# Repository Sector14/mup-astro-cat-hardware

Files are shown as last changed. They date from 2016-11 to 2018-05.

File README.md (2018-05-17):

# MUP Astro CAT

The MUP Astro CAT is an auto GPIO configuring add-on board for the
Raspberry PI 3 which provides additional hardware interfaces to 
communicate and control a Meade Autostar, Moonlite focuser and
temperature sensors.

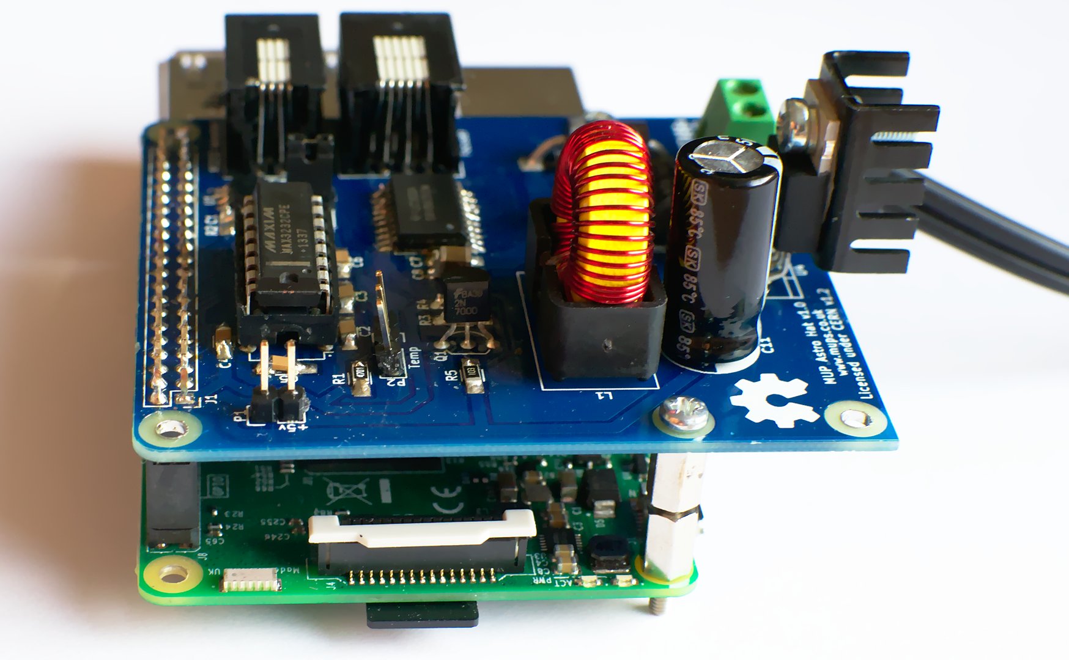
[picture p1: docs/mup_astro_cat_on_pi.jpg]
MUP Astro Hat


This repository contains the hardware project files needed to build 
the MUP Astro CAT. Firmware and the INDI driver is available in a separte
repo:

  https://github.com/Sector14/mup-astro-cat

Please refer to the additional documentation in the docs/ directory for
information on port pinouts for cables and hardware testing notes.

CAT refers to the Schmidt-Cassagrain telescope (CAT for short) this board will
be attached to. After naming it CAT I considered the recursive "CAP" which
would stand for "CAP Attached on Pi" since this project doesn't quite meet
the "Hat" spec, a cap is not a hat! but that means renaming things so CAT it is.

# Directories

  * control_cat - Kicad project incl schematic/pcb layout for the MUP Astro Cat. (CERN)
  * docs        - Documentation and 3rd party datasheets
  * gerber      - Exported gerber files for re-ordering PCBs

# Intended Purpose

Use a raspberry pi and additional interface board to control the 
following devices:

  * SXVR-H9
  * LodeStar
  * Filter Wheel
  * LX90 Handset
  * Moonlite Focuser
  * Illuminated Reticle (v2?)
  * Temp Sensor

The SXVR-H9, LodeStar (excl ST4 guide port) and Filter Wheel simply 
connect as USB devices to the Pi. 

The LX90 Handset uses a RS232 connection via RJ22 to the PI.

Moonlite focuser controlled via GPIO to a unipolar stepper
motor controller that will handle signal timing. Ensures any 
jitter/pauses from pi due to non realtime OS won't impact
motor control.

ST4 port from APM is not implemented, it might be added in a future
revision via i2c bus however as the LX90 supports pulse commands
over serial, it may not be needed.

# Library Setup

In addition to the libraries, modules and models that ship with Kicad,
this project also uses the MUP Kicad Library for additional parts and
an optional 3rd party 3D model library.

## Eeschema

If you receive a "The following libraries were not found:" message when
opening the schematic then you do not have the MUPS Kicad library available.
Kicad will use a cached copy of the library so this step is optional, but 
if you wish to make changes you should clone the repo:

  https://github.com/Sector14/mup-kicad-library

and add its location "Preferences/Component Libraries" as a user defined 
search path in the "parts library editor".  Then close and re-open Eeschema
and all the schematic symbols should now be found.

## Footprints

The above repo also contains footprint files for PCBNew in the modules/
directory and 3d models (where applicable). PCBNew will need each modules/\*.pretty
directory adding to the global library, or if you prefer, the project specific 
libraries.

To do so, open PCBNew, "Preferences/Footprints Libraries Manager", then 
"Append with Wizard" and select each ".pretty" directory and click Next, then
select whether to add the footprint to the global or project library.

Note: Some footprints are unchanged Kicad footprints that have only been
saved to the MUPS library in order to associate a 3d model with the footprint.
If the official Kicad library ever adds the missing models, the parts will
likely be removed from this repo.

## 3d Models

Some parts include a reference to models from the GPL'd 3d library by "kcswalter".
These are optional models and not included in the MUPS Kicad library.

If you checkout the walter repo from

  git://smisioto.eu/kicad_libs.git 

You can have Kicad use these models during 3d preview mode
by adding a new env variable in PCBNew "Preferences/Configure Paths" 
called WALTER_KI3DMOD and with the path set to the 
<walter repo checkout path>/modules/packages3d/ directory. 

Any footprints in the MUPS library that has the 3d model path prefixed 
with {WALTER_KI3DMOD}/walter/ will then use the appropriate 3D model.
The same will apply to {MUPS_KI3DMOD}/mups/ although at this time I've
yet to create any custom 3D models and find it unlikely I will

# Gerber Export

For Ordering PCBs from dirtypcbs.com

For "plotting":-

  * "Gerber" format is selected.
  * Select Layers F.Cu, B.Cu, F.SilkS, B.Mask, F.Mask, Edge.Cuts
  * Select Options:
   * Plot footprint values
   * Plot footprint references
   * Exclude PCB edge layer from other layers
  * Select Gerber Options:
   * User Protel filename extensions

For Drill file:

  * Units Inches
  * Zeros Format, Suppress leading zeros
  * Drill Map File Format (not used)
  * Drill File Options:
   * Minimal header
   * Merge PTH and NPTH holes into one file
  * Drill origin, Absolute

After export, rename the edge cuts "gm1" extension to "gml" prior
to uploading zip to dirtypcbs.com.

# Future Revision

Selecting surface 1206 style footprint for C8, the 100uF bypass capacitor 
for the DRV8805 was a little costly due to needing higher than 12V. An 
SMD electrolytic would prove significantly cheaper £0.27 vs £2.46
and with a greater voltage margin and not require that much additional 
space for a radial footprint. Lapse in judgement to be corrected on a 
future revision.

The power supply could be reduced in size with a more carefully
selected inductor. Having never laid out a SMPS however, I decided
to stick to the recommended layout and inductors based on the
TI regulator used. Further experimentation will be done prior to
revision 2 along with a change to SMD electrolytics and diodes.

A surface mounting socket to mate the CAT to the pi would be a better
choice as it allows an extended pin leg header to be mounted to the
pi and then the CAT mounted on top. This works out cheaper than the
elevated sockets.

Signal lines all need test point locations making available.

Switch 4p4c and 6p6c connector layout to socket mounting 
to allow panel mount option or in the case of a direct wiring, a
smaller connector area.

USB ideally should also be panel mount but desoldering the PI's
dual sockets is something I'd prefer to avoid.

ST3232 switch to soic version.

Add pin labels to silkscreen for temp port etc current broken square for
ground is too hard to see once a pin header is soldered in place.

Add a via behind the regulator to connect ground planes for better
thermal relief.

HAT specs for back-powering via 5V GPIO header pin requires addition
of an ideal 'safety' diode see [design guide](https://github.com/raspberrypi/hats/blob/master/designguide.md)

# Reference

  * https://github.com/raspberrypi/hats
  * https://github.com/raspberrypi/hats/blob/master/designguide.md
  * https://github.com/xesscorp/RPi_Hat_Template
  * http://www.briandorey.com/post/Raspberry-Pi-3-UART-Boot-Overlay-Part-Two

# Copyright

Copyright Gary Preston 2016.

This documentation describes Open Hardware and is licensed under the
CERN OHL v. 1.2.

You may redistribute and modify this documentation under the terms of the
CERN OHL v.1.2. (http://ohwr.org/cernohl). This documentation is distributed
WITHOUT ANY EXPRESS OR IMPLIED WARRANTY, INCLUDING OF
MERCHANTABILITY, SATISFACTORY QUALITY AND FITNESS FOR A
PARTICULAR PURPOSE. Please see the CERN OHL v.1.2 for applicable
conditions

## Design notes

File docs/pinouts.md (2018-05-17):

# Pinouts

## Pi Hat RS232

Looking into port, locking tab on bottom, left to right:-

  1. GND
  2. NC
  3. Tx
  4. Rx

## Autostar RS232 Port

Looking into port with locking tab on bottom, left to right:- 

  * GND
  * NC
  * Tx
  * Rx

Note: Tx and Rx should cross over in cable so Tx on PC is Rx on Autostar.

## Moonlite Focuser

    Model: LSG35012F76P
    Voltage: 12v
    Resistance/Phase: 65.0 Ohm
    Inductance H/Phase: 27.0
    Hold Current: 0.369A
    Total Input Watt: 4.5
    Min Holding Torque: 420 gf-cm (6.3 oz/in)
    Pull out Torque @ 175p/s: 151 gf-cm (2.1 oz-in)
    Detent Torque: 130 gf-cm (1.8 oz-in)
    Rotor inertia: 6.8 gf-cm^2 (0.372 oz-in^2)
    Weight: 82g (2.9oz)
    Length: 22mm (0.866in)

|Part No.     | Similar | Step Angle Degrees | Steps Per Revolution | Reduction | Nominal Voltage VDC | Min Holding Torque (oz-in)| Pull-out Torque @175p/s (oz-in) | Detent Torque (oz-in) | Rotor Inertia (oz-in) | Weight (oz) | Length (in) |
|LSG35012F76P |3004-003 |0.100 |3600 |75 |12 |150 |101 |150.0 |0.0372 |8.6 |1.55

Looking into 6p6c port on Pi Hat, locking tab on bottom, left to right:-

  1. 12v
  2. Out1
  3. Out2
  4. Out3
  5. Out4
  6. No connect

The moonlite focuser uses a DB9 connector with the following pin mapping:-

  1. O1 (coil 1+)
  2. O2 (coil 1-)
  3. O3 (coil 2+)
  4. O4 (coil 2-)
  5. 12v
  6-9 NC

The cable itself however cannot be a straight out1 -> O1, out2 -> O2 connection
as the stepping sequence the motor expects uses a different coil connection to the
out1..4 sequence. The cable needs to be:-

  Board Side -> DB9 Side
  1. 12v  -> 12v
  2. Out4 -> O3
  3. Out3 -> O2
  4. Out2 -> O4
  5. Out1 -> O1

           > DB9 Side
  1. 12v  -> 12v
  2. Out1 -> O1
  3. Out2 -> O4
  4. Out3 -> O2
  5. Out4 -> O3

# Reference

  * http://www.beckwithelectronics.com/HURST/LSG35012F76P.htm
  * http://www.weasner.com/etx/techtips/2007/aux-port.html
  * http://www.weasner.com/etx/archive/mar12/autostar.html

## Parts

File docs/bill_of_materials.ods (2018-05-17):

MUP Astro Hat V1.0 – Bill of Materials
Reference | Value | Qty | Footprint | Datasheet | Cost/item | Mouser | Farnell | Toby | Sparkfun
C1-C7,C10 | 0.1uF | 8 | Capacitors_SMD:C_1206_HandSoldering |  | £0.07 | 581-12065C104K |  |  |  |  | £0.56
C8 | 100uF | 1 | Capacitors_SMD:C_1206_HandSoldering |  | £2.95 |  | 2309033 |  |  |  | £2.95
C9 | 100uF | 1 | Capacitors_ThroughHole:C_Radial_D6.3_L11.2_P2.5 |  |  |  |  |  |  |  | £0.00 | already in stock
C11 | 1000uF | 1 | Capacitors_ThroughHole:C_Radial_D10_L16_P5 |  |  |  |  |  |  |  | £0.00 | already in stock
D2,D3 | 1N5822 | 2 | Diodes_ThroughHole:Diode_DO-201AD_Horizontal_RM15 |  | £0.14 |  | 9801243 |  |  |  | £0.28
J1 | RPi_GPIO | 1 | mups_connect:PI_Pin_Header_Straight_2x20 |  |  |  |  |  |  |  | £0.00
JP1 | Jumper_NO_Small | 1 | Connect:PINHEAD1-2 |  |  |  |  |  |  |  | £0.00 | already in stock
L1 | 100uH | 1 | mups_assorted:Choke_Toroid_8x16mm_Vertical |  | £4.32 |  | 2215967 |  |  |  | £4.32
P1 | 5V Reticle | 1 | Pin_Headers:Pin_Header_Straight_1x02 |  |  |  |  |  |  |  | £0.00 | already in stock
P2 | DS18B20 | 1 | Pin_Headers:Pin_Header_Straight_1x03 |  |  |  |  |  |  |  | £0.00 | already in stock
P3 | LX90 HBX | 1 | mups_connect:4P4C |  | £0.55 | 571-1-1705949-1 |  |  |  |  | £0.55
P4 | Focuser Motor | 1 | mups_connect:6P6C |  | £0.14 | 806-MP66X-1000 |  |  |  |  | £0.14
P5 | 12V In | 1 | mups_connect:Terminal_Block_5mm_2 |  | £0.26 | 571-282836-1 |  |  |  |  | £0.26
Q1 | 2N7000 | 1 | TO_SOT_Packages_THT:TO-92_Inline_Wide |  |  |  |  |  |  |  | £0.00 | already in stock
R1 | 4k7 | 1 | Resistors_SMD:R_1206_HandSoldering |  | £0.02 | 667-ERJ-8ENF4701V |  |  |  |  | £0.02
R2-R5 | 10k | 4 | Resistors_SMD:R_1206_HandSoldering |  | £0.05 | 588-AS12J1002ET |  |  |  |  | £0.20
R6 | 3k1 | 1 | Resistors_SMD:R_1206_HandSoldering |  | £0.01 |  | 2138387 |  |  |  | £0.01
R7 | 1k | 1 | Resistors_SMD:R_1206_HandSoldering |  | £0.05 | 588-AS12J1001ET |  |  |  |  | £0.05
U1 | 24C32 | 1 | Housings_SOIC:SOIC-8_3.9x4.9mm_Pitch1.27mm |  | £0.35 | 698-CAT24C32WI-GT3 |  |  |  |  | £0.35
U2 | ST3232 | 1 | Housings_DIP:DIP-16_W7.62mm |  | £6.07 |  | 2511858 |  |  |  | £6.07
U3 | DRV8805 | 1 | Housings_SOIC:SOIC-20_7.5x12.8mm_Pitch1.27mm |  | £3.06 | 595-DRV8805DW |  |  |  |  | £3.06
U4 | LM2576 | 1 | TO_SOT_Packages_THT:Pentawatt_Neutral_Staggered_Verical_TO220-5-T05D |  | £1.83 |  | 2318511 |  |  |  | £1.83
 |  |  |  |  |  |  |  |  |  |  | £20.65
MUP Astro Hat V1.0 – Project Extras
Reference | Value | Qty | Description | Datasheet | Cost/item | Mouser | Farnell | Toby | Sparkfun |  | Total
Box | 120x120x60 | 1 | Project Box |  | £7.32 |  | 4436910
 | PI3 | 1 | Raspberry PI 3 |  |  |  |  |  |  |  |  | already in stock
 |  | 1 | Heat Sink |  | £0.17 |  | 1703172 |  |  |  | £0.17
 |  | 1 | Amphenol 4 Pin connector housing |  | £1.10 |  | 2361184 |  |  |  | £1.10
 |  | 4 | 18awg contact male |  | £0.22 |  | 2361202 |  |  |  | £0.86
 |  | 1 | Wedgelock plug |  | £0.20 |  | 2361198 |  |  |  | £0.20
 |  | 1 | Amphenol 4 Pin receptacle |  | £1.13 |  | 2361178 |  |  |  | £1.13
 |  | 4 | 18awg contact female |  | £0.60 |  | 2361203 |  |  |  | £2.40
 |  | 1 | Wedgelock receptacle |  | £0.22 |  | 2361192 |  |  |  | £0.22
 |  | 3 | 18AWG 4 core power cable, hi flex < -20c |  | £5.18 |  | 1286025 |  |  |  | £15.55
 |  | 2 | 24AWG 5 core shielded motor cable |  | £2.89 |  | 1218693 |  |  |  | £5.78
 |  | 1 | 6 pin chassis socket & plug |  | £2.40 |  |  |  | PRT-11475 |  | £2.40
 |  | 1 | DC 2.1mm Plug (SXVR cable) |  | £0.91 |  | 2455456 |  |  |  | £0.91
 |  | 2 | DC 2.5mm plug |  |  |  |  |  |  |  | £0.00 | already in stock
 |  | 4 | DC 2.5mm panel mount socket |  | £1.44 |  | 2285054 |  |  |  | £5.76
 |  | 1 | Dsub 9 pin receptacle |  | £0.39 |  | 1345230 |  |  |  | £0.39
 |  | 1 | Dsub backshell (90 deg connection) |  | £1.81 |  | 2079365 |  |  |  | £1.81
 |  | 10 | Dsub contacts female |  | £0.08 |  | 2293759 |  |  |  | £0.84
 |  | 1 | USB dust cap (for water ingress on unused ports) |  | £0.46 |  | 1908442 |  |  |  | £0.46
 |  | 10 | Fixing screws |  | £0.14 |  | 520160 |  |  |  | £1.44
 |  | 1 | DirtyPCB Order (was min 10 boards I.e £22 though) |  | £2.20 |  |  |  |  |  | £2.20
 |  | 4 | M2.5 Spacer 8mm high |  | £0.09 |  |  | VBMP-M2.5-5.0-08 |  |  | £0.36
 |  | 4 | M2.5 nut |  | £0.02 |  | 1419446 |  |  |  | £0.06
 |  | 4 | M2.5 screws |  | £0.01 |  |  | 2333M256MM |  |  | £0.03
 |  |  | assorted usb cables and connectors like 4p4c, 6p6c |  |  |  |  |  |  |  | £44.08
 |  |  |  |  |  |  |  |  |  | Final Cost | £64.73
NOTE: This list of materials includes all items needed for v1.0 of the PCB although some items I already had in stock and did not need to order. For those an order code has been added as a guide. Project extras are items needed for the overall project such as cables, box, mounting screws etc

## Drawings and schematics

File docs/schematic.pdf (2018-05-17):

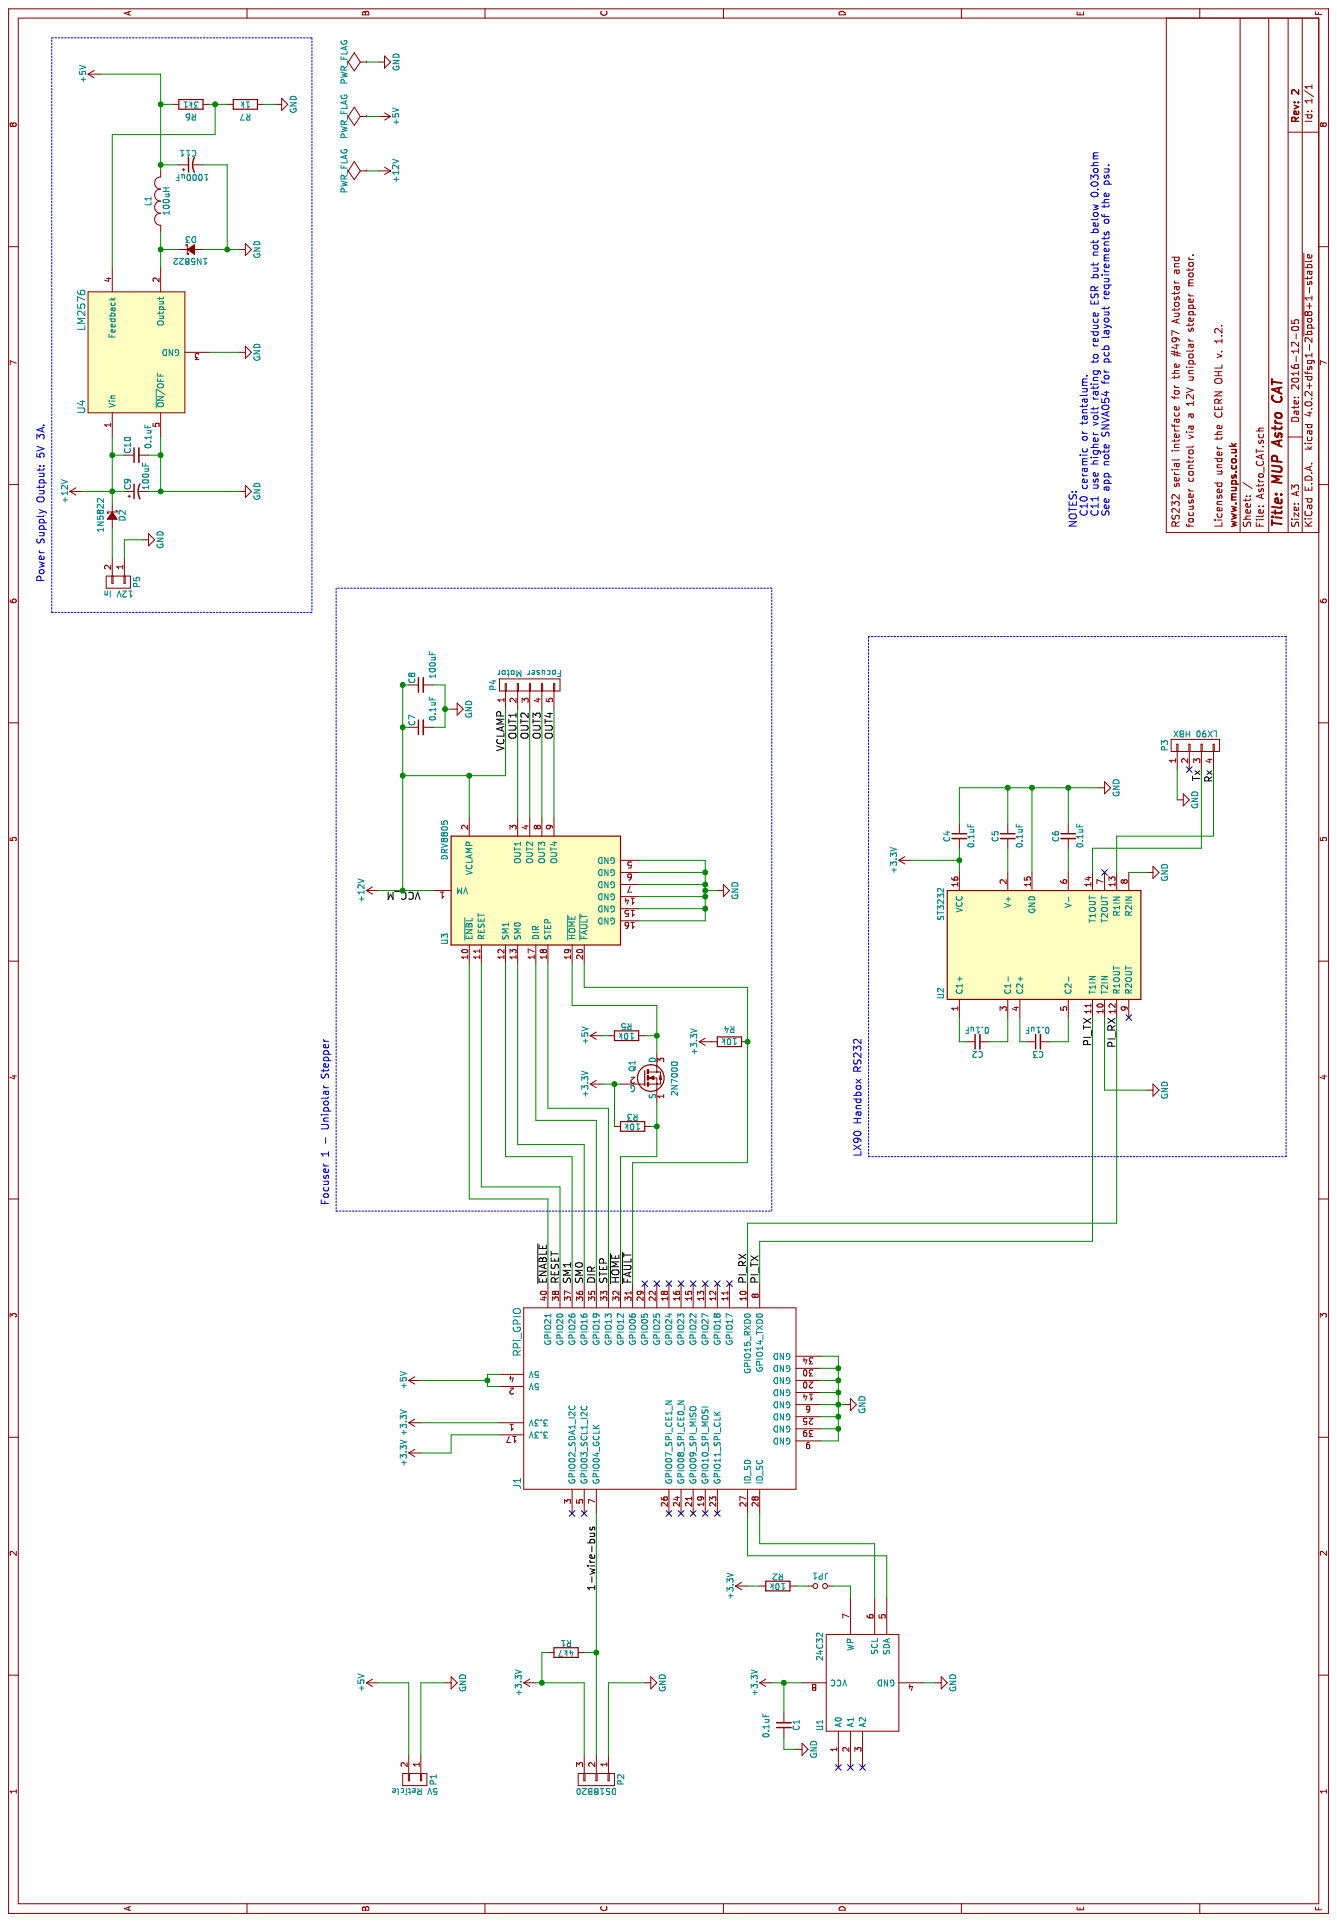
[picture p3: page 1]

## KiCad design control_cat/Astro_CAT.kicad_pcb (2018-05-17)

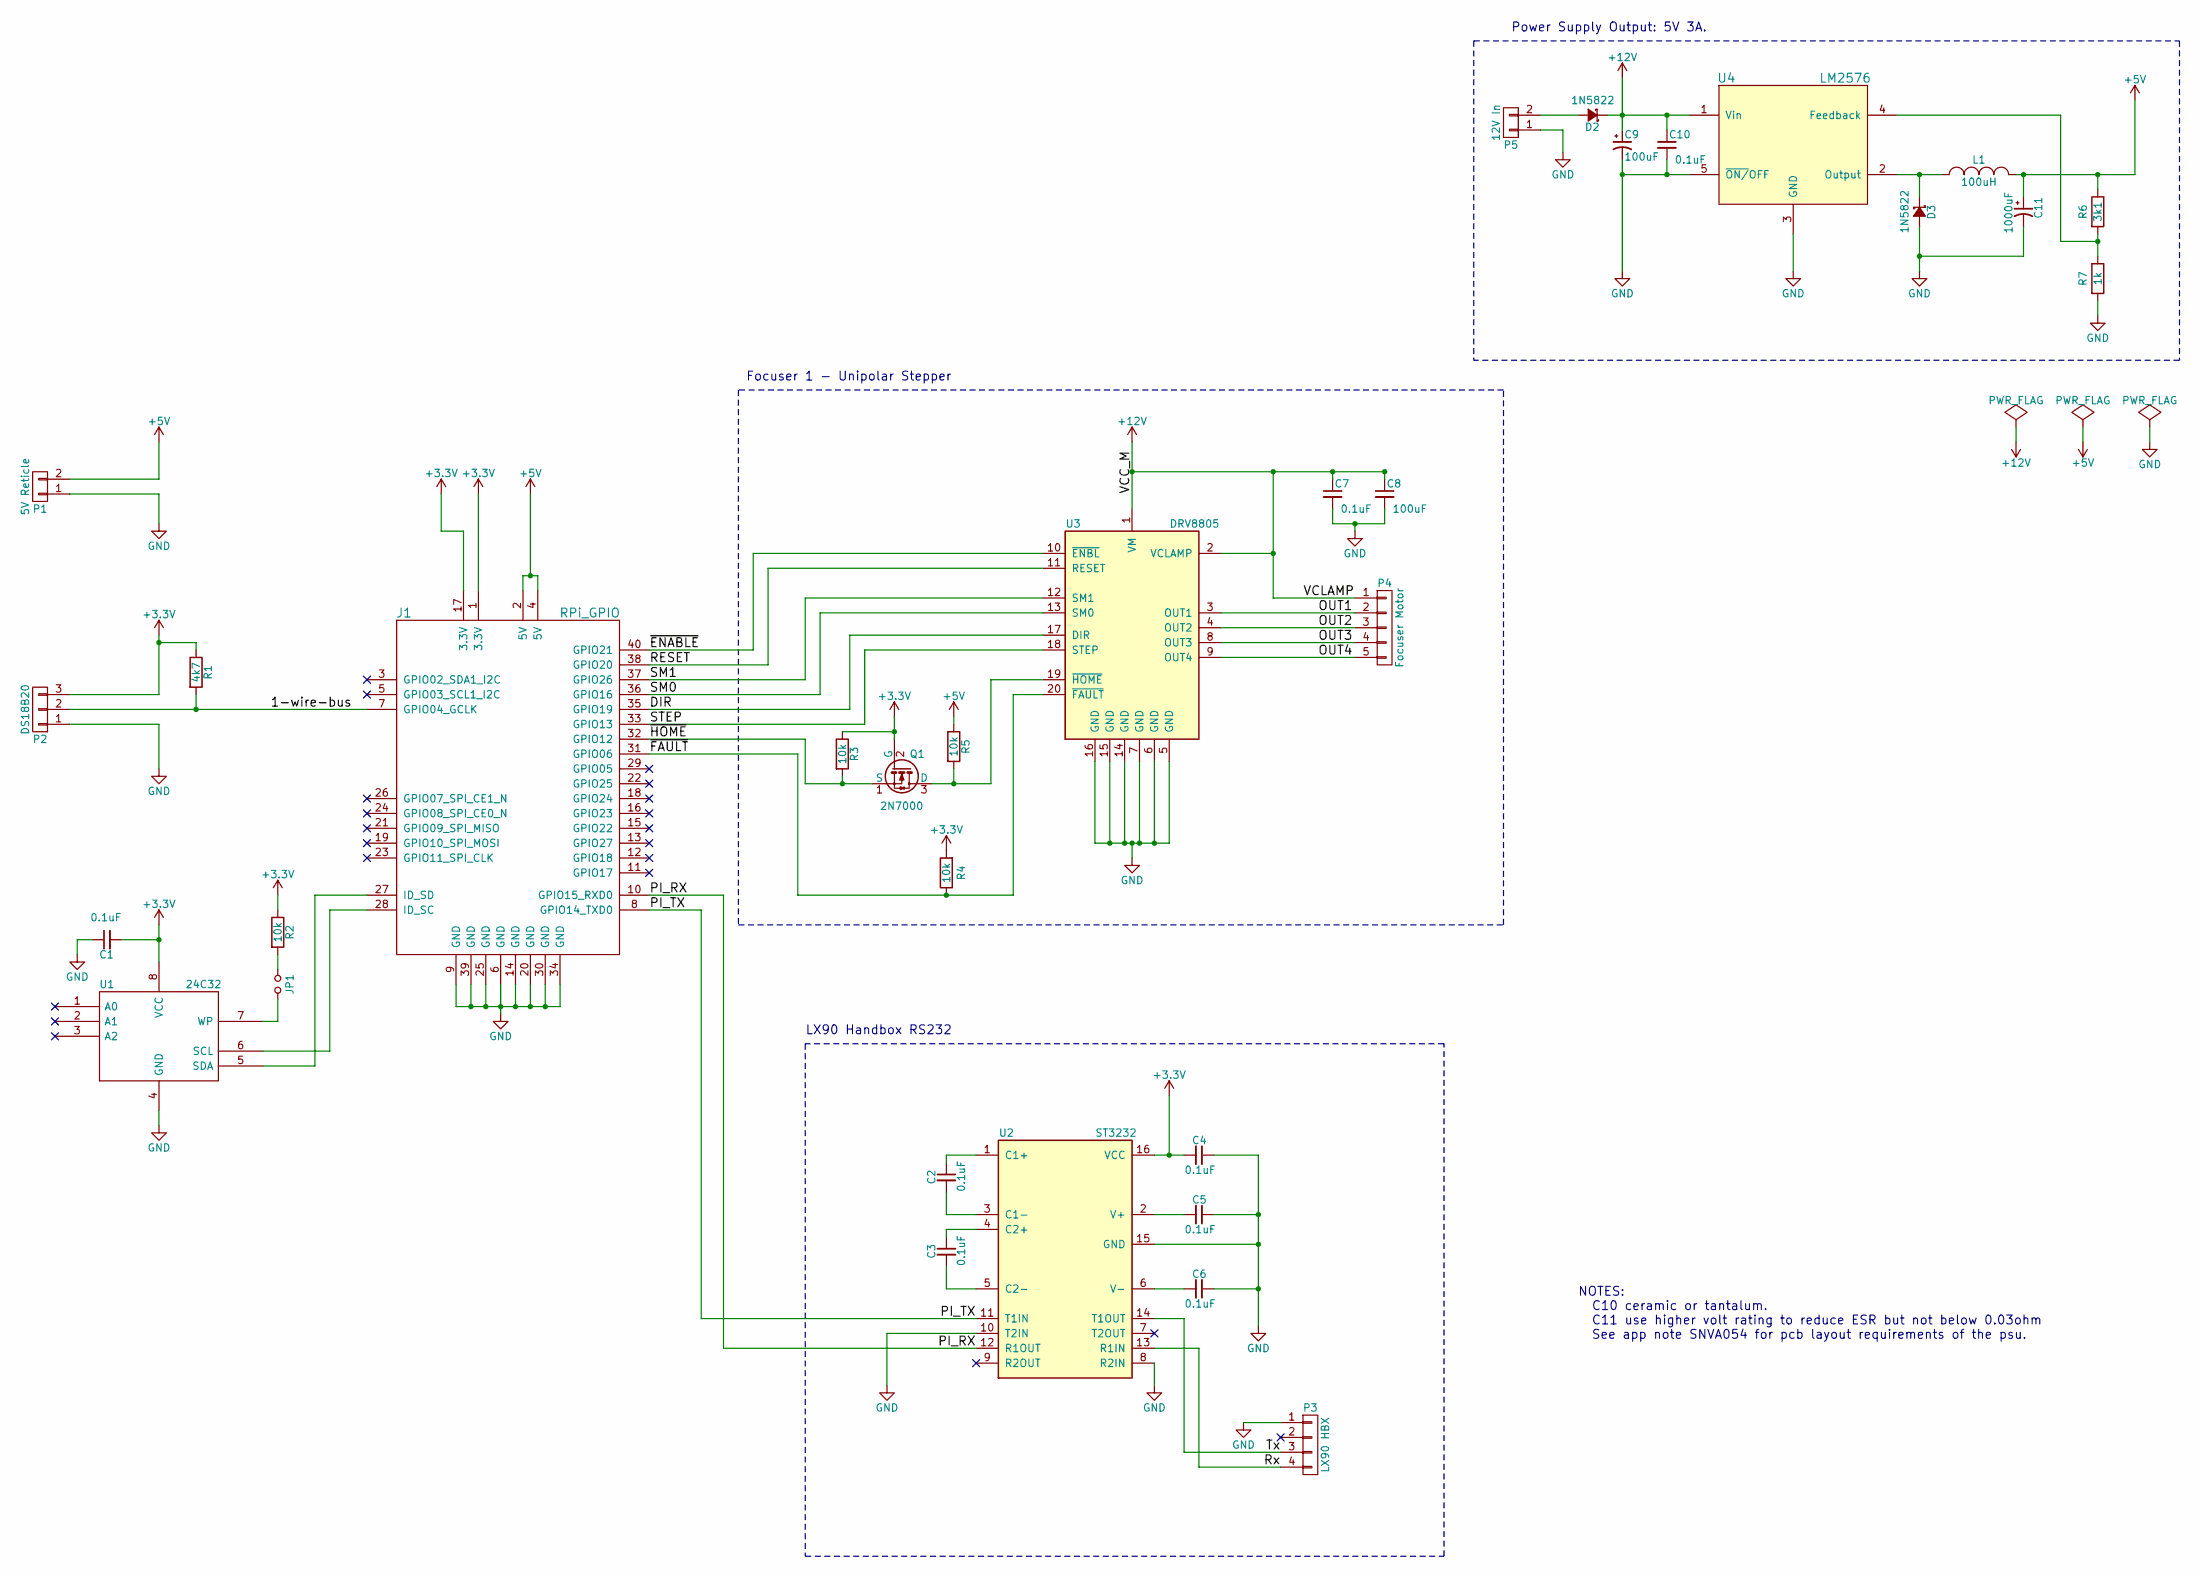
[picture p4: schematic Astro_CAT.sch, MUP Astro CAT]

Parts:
C1, C2, C3, C4, C5, C6, C7, C10: 0.1uF; C_1206_HandSoldering
C8: 100uF; C_1206_HandSoldering
C9: 100uF; C_Radial_D6.3_L11.2_P2.5
C11: 1000uF; C_Radial_D10_L16_P5
D2, D3: 1N5822; Diode_DO-201AD_Horizontal_RM15
J1: RPi_GPIO; PI_Pin_Header_Straight_2x20
JP1: Jumper_NO_Small; PINHEAD1-2
L1: 100uH; Choke_Toroid_8x16mm_Vertical
P1: 5V Reticle; Pin_Header_Straight_1x02
P2: DS18B20; Pin_Header_Straight_1x03
P3: LX90 HBX; 4P4C
P4: Focuser Motor; 6P6C
P5: 12V In; Terminal_Block_5mm_2
Q1: 2N7000; TO-92_Inline_Wide
R1: 4k7; R_1206_HandSoldering
R2, R3, R4, R5: 10k; R_1206_HandSoldering
R6: 3k1; R_1206_HandSoldering
R7: 1k; R_1206_HandSoldering
U1: 24C32; SOIC-8_3.9x4.9mm_Pitch1.27mm
U2: ST3232; DIP-16_W7.62mm
U3: DRV8805; SOIC-20_7.5x12.8mm_Pitch1.27mm
U4: LM2576; Pentawatt_Neutral_Staggered_Verical_TO220-5-T05D

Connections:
+3V3: C1.2, C4.2, J1.1 (3.3V), J1.17 (3.3V), P2.3, Q1.2 (G), R1.1, R2.1, R3.1, R4.2, U1.8 (VCC), U2.16 (VCC)
+5V: C11.1, J1.2 (5V), J1.4 (5V), L1.2, P1.2, R5.1, R6.1
+12V: C7.1, C8.1, C9.1, C10.1, D2.1 (K), P4.1, U3.1 (VM), U3.2 (VCLAMP), U4.1 (Vin)
/1-wire-bus: J1.7 (GPIO04_GCLK), P2.2, R1.2
/DIR: J1.35 (GPIO19), U3.17 (DIR)
/OUT1: P4.2, U3.3 (OUT1)
/OUT2: P4.3, U3.4 (OUT2)
/OUT3: P4.4, U3.8 (OUT3)
/OUT4: P4.5, U3.9 (OUT4)
/PI_RX: J1.10 (GPIO15_RXD0), U2.12 (R1OUT)
/PI_TX: J1.8 (GPIO14_TXD0), U2.11 (T1IN)
/RESET: J1.38 (GPIO20), U3.11 (RESET)
/Rx: P3.4, U2.13 (R1IN)
/SM0: J1.36 (GPIO16), U3.13 (SM0)
/SM1: J1.37 (GPIO26), U3.12 (SM1)
/STEP: J1.33 (GPIO13), U3.18 (STEP)
/Tx: P3.3, U2.14 (T1OUT)
/~ENABLE: J1.40 (GPIO21), U3.10 (~ENBL)
/~FAULT: J1.31 (GPIO06), R4.1, U3.20 (~FAULT)
/~HOME: J1.32 (GPIO12), Q1.1 (S), R3.2
GND: C1.1, C4.1, C5.1, C6.1, C7.2, C8.2, C9.2, C10.2, C11.2, D3.2 (A), J1.6 (GND), J1.9 (GND), J1.14 (GND), J1.20 (GND), J1.25 (GND), J1.30 (GND), J1.34 (GND), J1.39 (GND), P1.1, P2.1, P3.1, P5.1, R7.2, U1.4 (GND), U2.8 (R2IN), U2.10 (T2IN), U2.15 (GND), U3.5 (GND), U3.6 (GND), U3.7 (GND), U3.14 (GND), U3.15 (GND), U3.16 (GND), U4.3 (GND), U4.5 (~ON/~OFF)
unnamed: C2.1, U2.1 (C1+)
unnamed: C2.2, U2.3 (C1-)
unnamed: C3.1, U2.4 (C2+)
unnamed: C3.2, U2.5 (C2-)
unnamed: C5.2, U2.2 (V+)
unnamed: C6.2, U2.6 (V-)
unnamed: D2.2 (A), P5.2
unnamed: D3.1 (K), L1.1, U4.2 (Output)
unnamed: J1.27 (ID_SD), U1.5 (SDA)
unnamed: J1.28 (ID_SC), U1.6 (SCL)
unnamed: JP1.1, R2.2
unnamed: JP1.2, U1.7 (WP)
unnamed: Q1.3 (D), R5.2, U3.19 (~HOME)
unnamed: R6.2, R7.1, U4.4 (Feedback)

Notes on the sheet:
LX90 Handbox RS232
Focuser 1 - Unipolar Stepper
Power Supply Output: 5V 3A.
NOTES: C10 ceramic or tantalum. C11 use higher volt rating to reduce ESR but not below 0.03ohm See app note SNVA054 for pcb layout requirements of the psu.

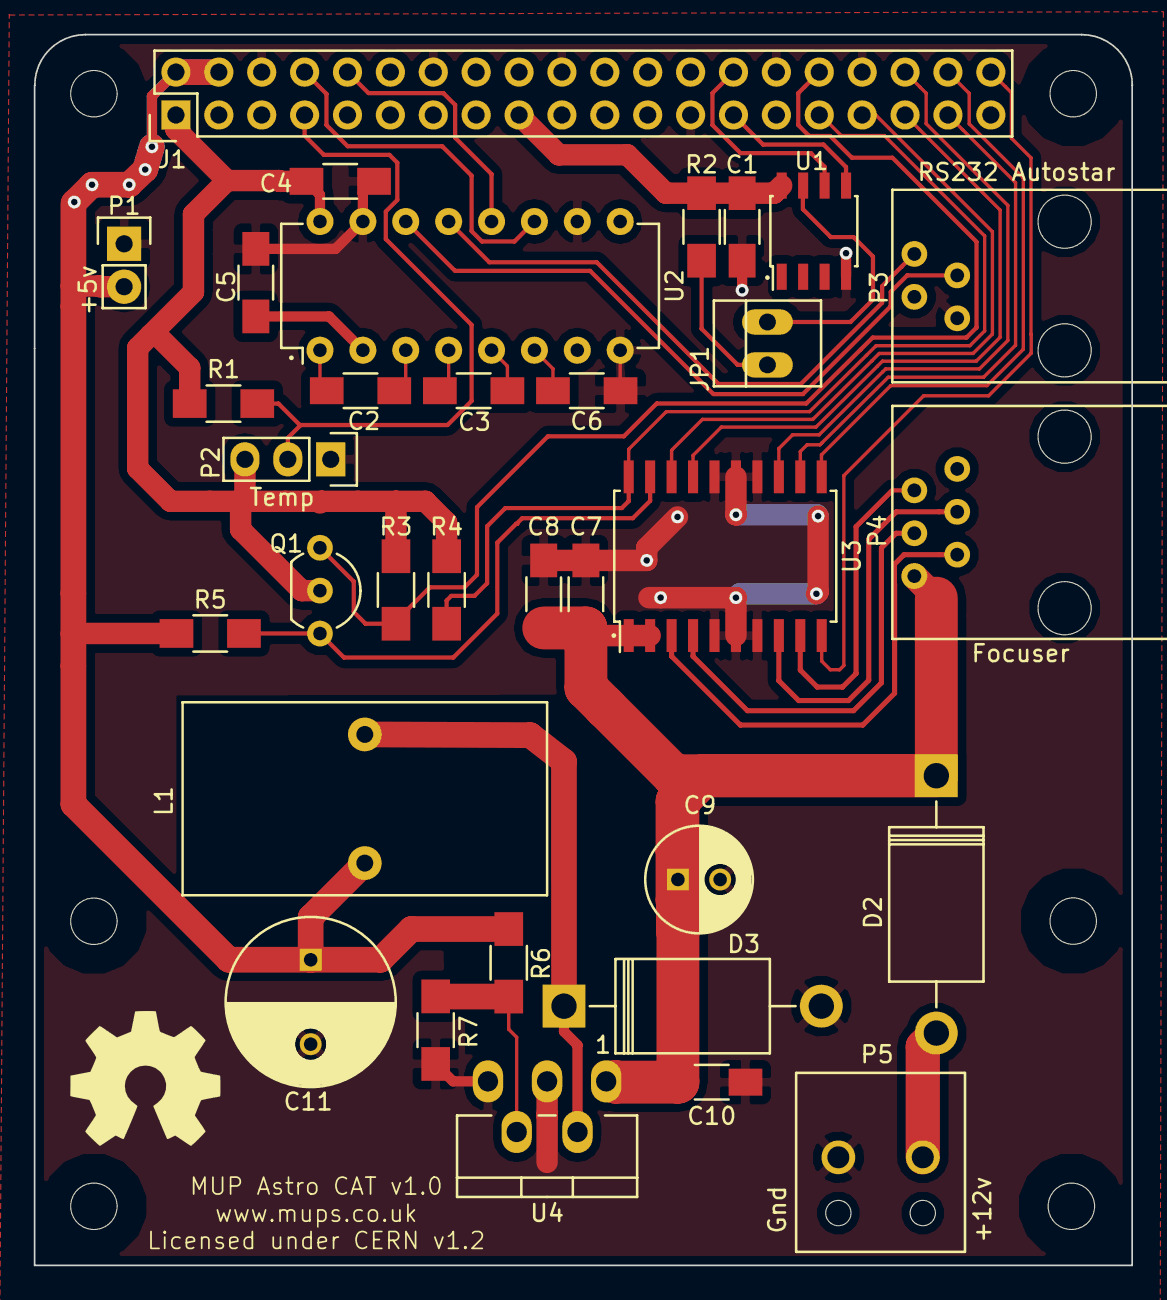
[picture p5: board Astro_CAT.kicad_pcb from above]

Board: 2 copper layers, 65.0 x 72.9 mm, 33 parts (0 on the bottom side), 35 nets.

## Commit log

2016-11-03 Initial checkin of mup astro hat schematic, pcb and associated reference datasheets.
    [RPi_Hat-B.Cu.gbl, RPi_Hat-B.Mask.gbs, RPi_Hat-F.Cu.gtl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]
2016-11-03 Add CERN OHW guide. Adjust wording on schematic. Add v1.0 PDF schematic to docs/ dir.
2016-11-03 Switch footprint pin 1 to 4 around for 4p4c to match 6p6c ordering.
2016-11-27 Fix voltage divider network r6/r7.
    [bill_of_materials.ods]
2016-11-28 Switch Q1 to specific component.
    Q1 switched to custom 2N7000 component with gate as pin 2 and S/D to match TO-92 1,2,3 pin ordering of actual package/footprint.
    Update PCB layout with gate (3.3v) now center pin.
2016-12-07 Swap labels for SM0 and SM1 on pi pin side.
2016-12-08 Update readme with kicad repo info and tweaked test script.
2016-12-10 Split docs. Add device overlay and eeprom settings.
2016-12-10 Rename Hat to CAT.
    Due to lack of back powering protection diode and board not meeting
    the HAT mechanical spec, renaming the project to CAT to avoid confusion.
    [Astro_CAT.kicad_pcb, Astro_CAT.sch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]
2017-01-30 Splitting hardware off to separate repo.
    Update pinout for cables.
    [bill_of_materials.ods]

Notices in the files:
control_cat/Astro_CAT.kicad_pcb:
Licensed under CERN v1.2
